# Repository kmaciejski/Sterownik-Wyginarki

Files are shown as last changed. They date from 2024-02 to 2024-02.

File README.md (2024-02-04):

# Projekt sterownika wyginarki do profili stalowych

## Dane Techniczne
- Low cost MCU STM32F030F4P6
- Ekran LCD alfanumeryczny podłączony do magistrali I2C
- Podłączenie klawiatury 12 przyciskowej zrealizowane na 2 rejstrach 74HC166N
- Zewnętrzna pamięć EEPROM na płytce PCB do zapamiętywania ustawień podłączona do magistrali I2C
- Podłączony enkoder z linią Zerującą obsługiwany na przerwaniach
- Wyprowadzone wyjścia przekaźnikowe do sterowania stycznikami silnika i wbudowane przekaźniki na płytce PCB
- Zasilanie zewnętrzne 12V i wbudowane regulatory napięcia dla logiki na płytce PCB

## Możliwości
- Funkcja Automatycznego startu maszyny
- Funkcja Autocofania 
- Funkcja pamięci nastaw (8 różnych nastaw do zapamiętania M1-M8)
- Wielopoziomowe menu
- Zaawansowana obsługa przycisków na klawiaturze m.in. przytrzymanie i autorepetycja

## Działający prototyp







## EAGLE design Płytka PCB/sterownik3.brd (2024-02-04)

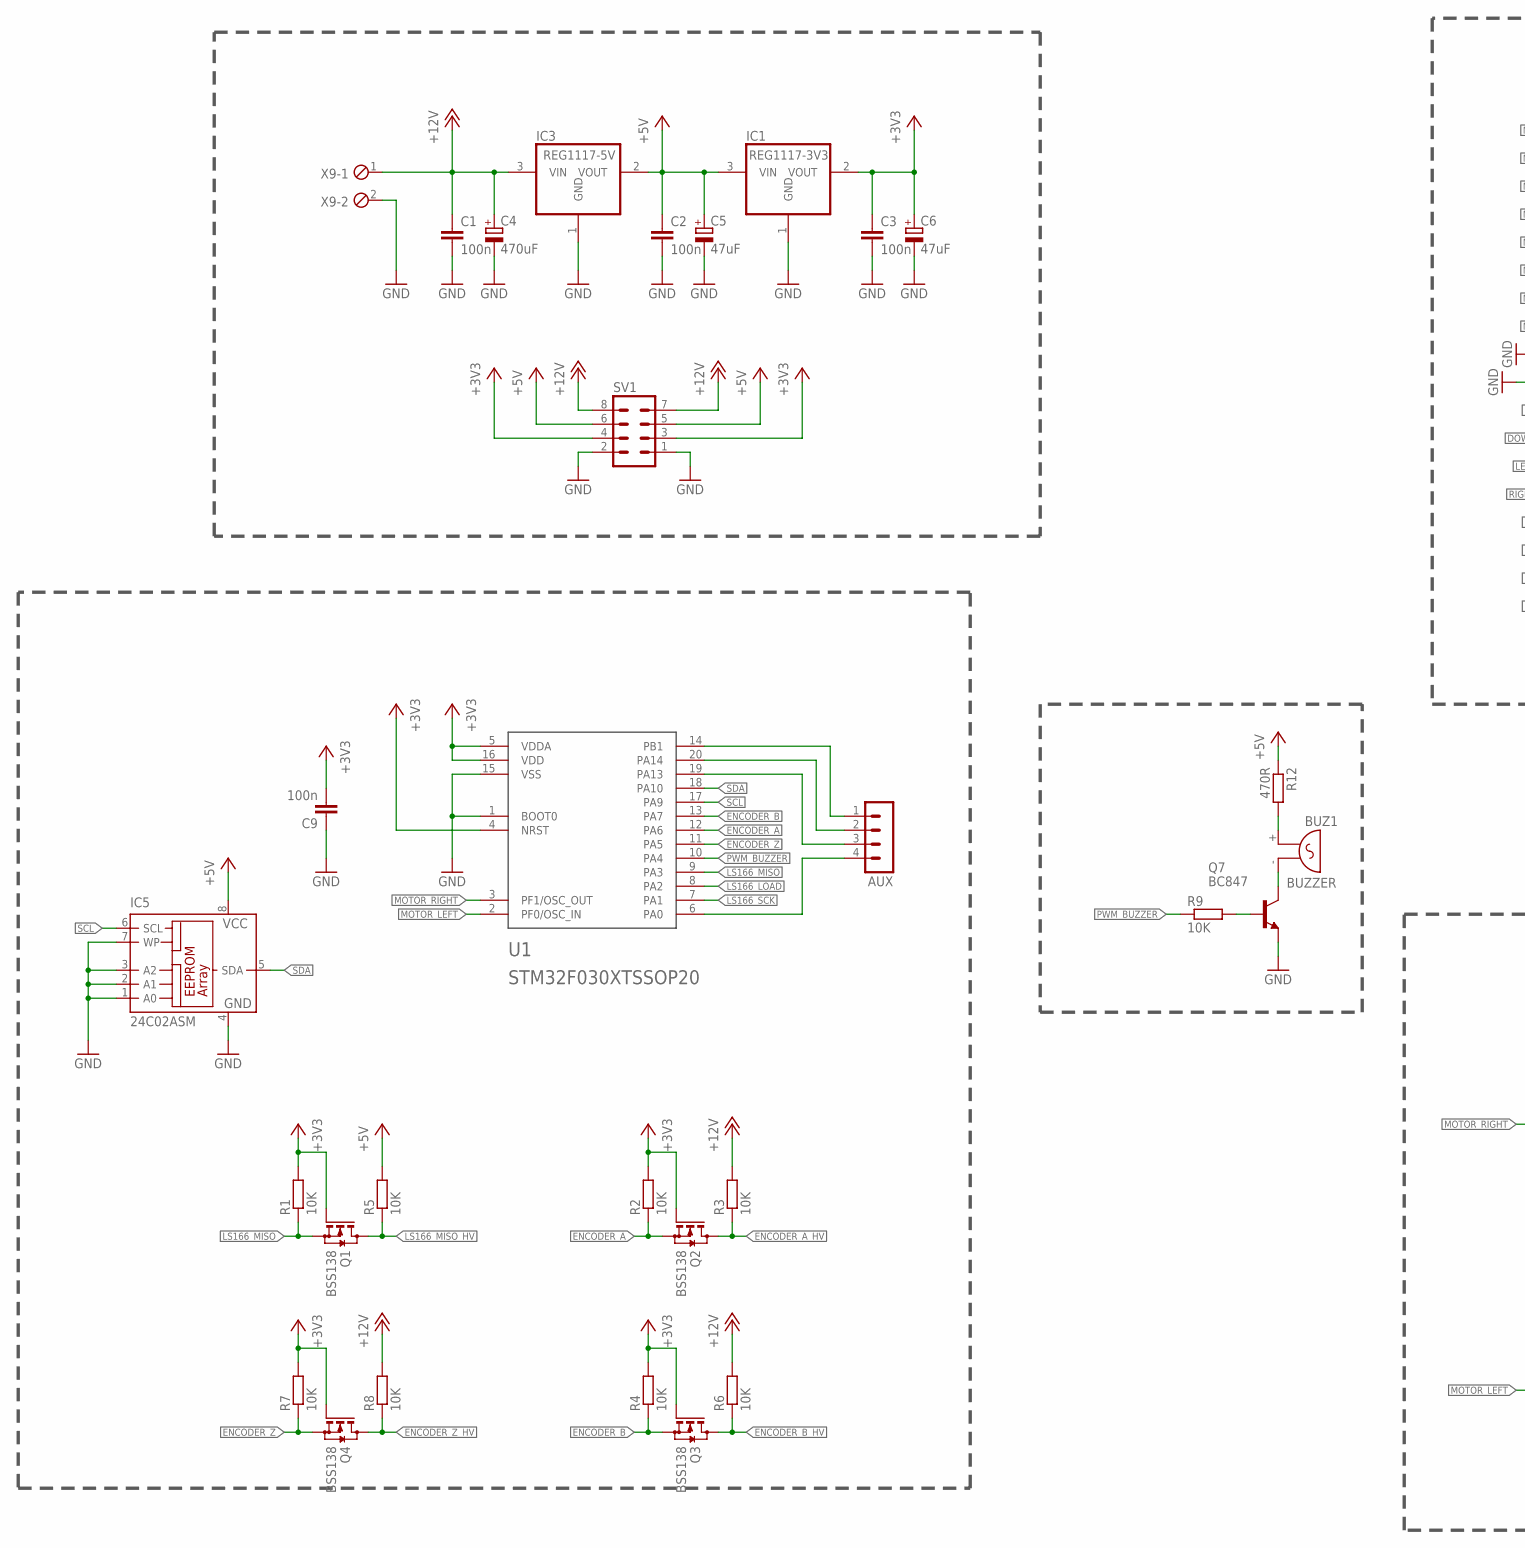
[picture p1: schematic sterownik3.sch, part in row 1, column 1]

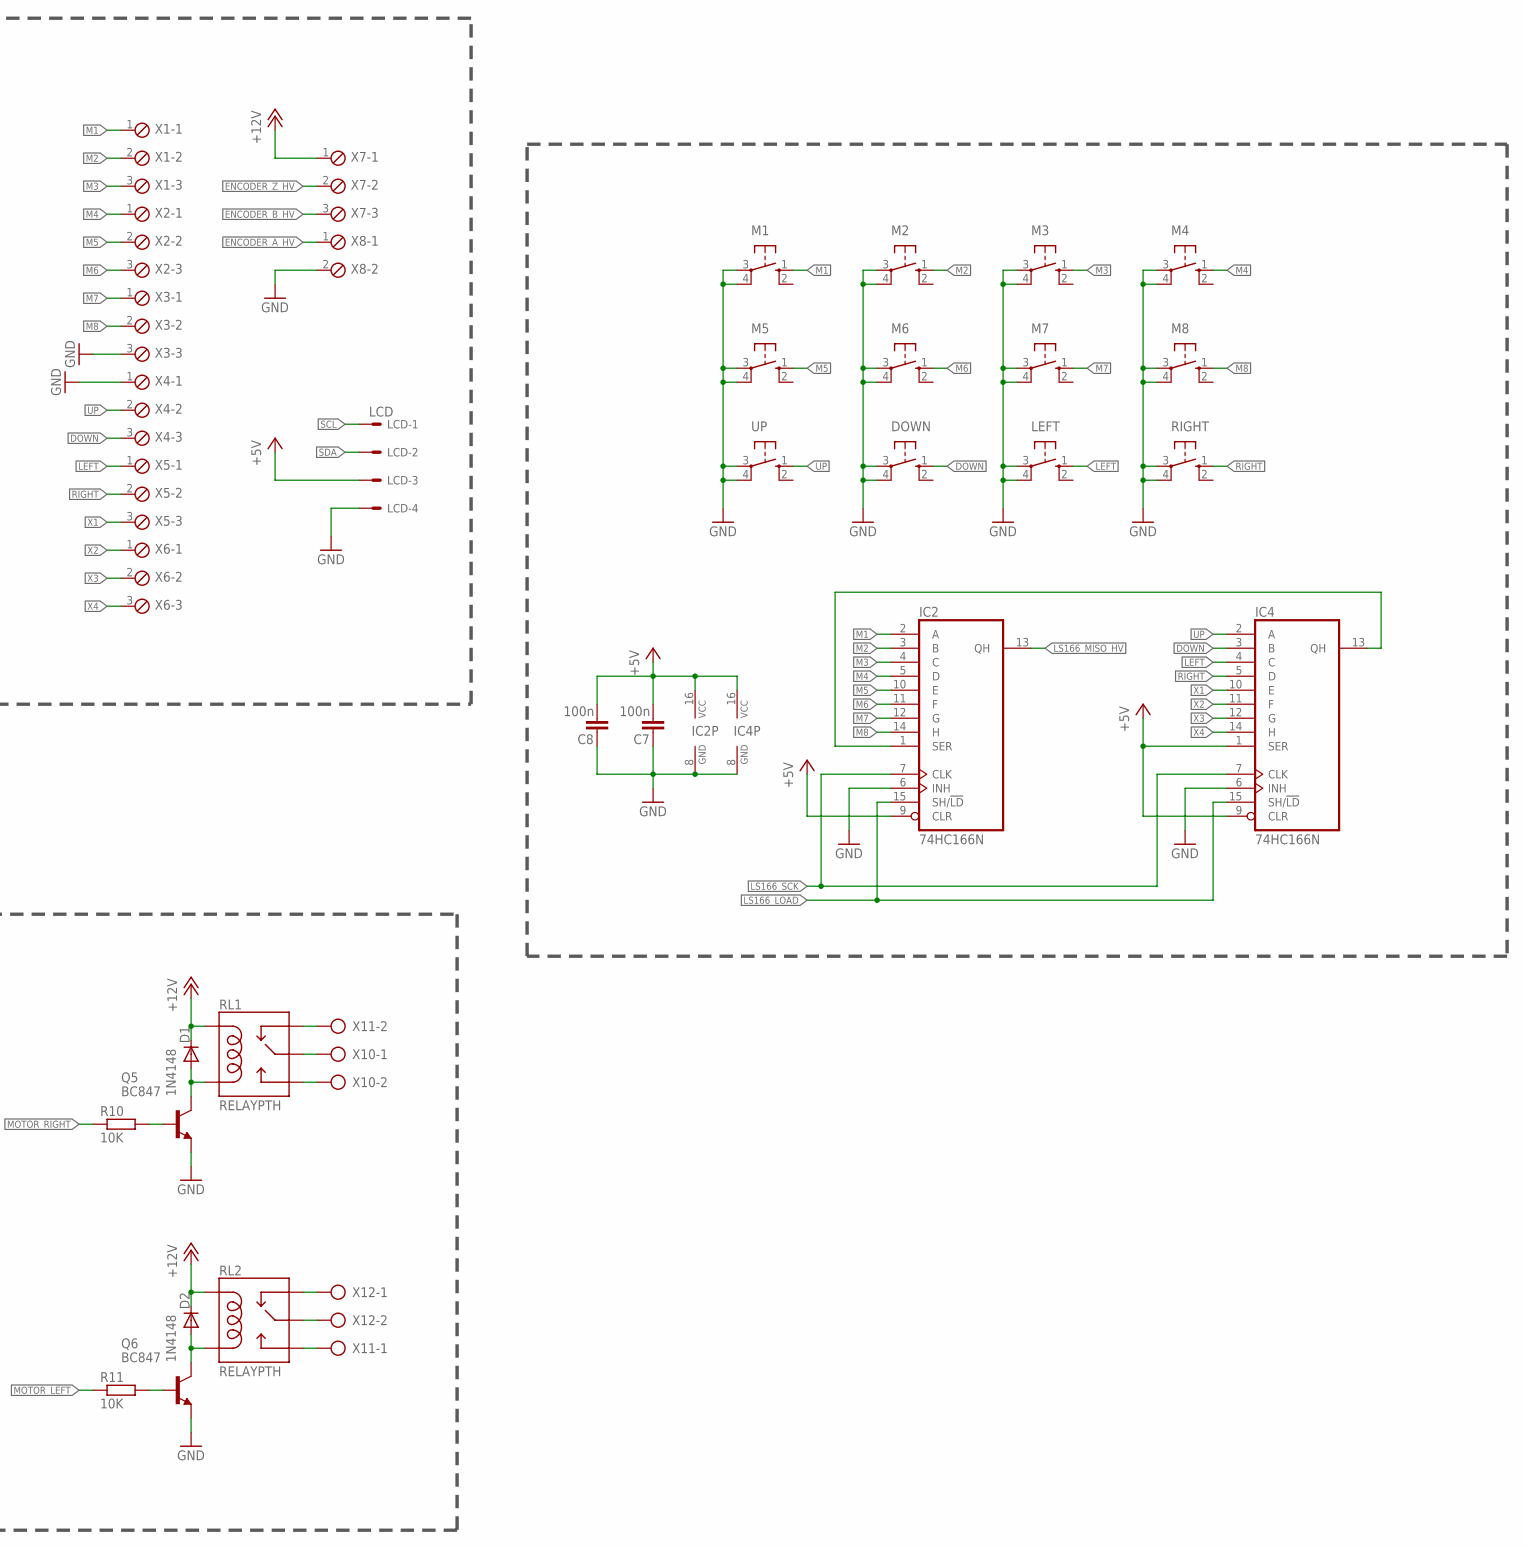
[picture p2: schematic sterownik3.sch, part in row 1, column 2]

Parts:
AUX: MA04-1
BUZ1: BUZZER; F/QMX
C1, C2, C3, C7, C8, C9: 100n; C0805
C4: 470uF; E5-8,5
C5, C6: 47uF; E5-6
D1, D2: 1N4148; DO35-7
DOWN: 10-XX; B3F-10XX
IC1: REG1117-3V3; SOT223
IC2, IC4: 74HC166N; DIL16
IC3: REG1117-5V; SOT223
IC5: 24C02ASM; SO-08M
LCD: LCD; 6410-04
LEFT: 10-XX; B3F-10XX
M1, M2, M3, M4, M5, M6, M7, M8: 10-XX; B3F-10XX
Q1, Q2, Q3, Q4: BSS138; SOT23
Q5, Q6, Q7: BC847; SOT23
R1, R2, R3, R4, R5, R6, R7, R8, R9, R10, R11: 10K; R0805
R12: 470R; R0805
RIGHT: 10-XX; B3F-10XX
RL1, RL2: RELAYPTH; SRD-05VDC-SL-C
SV1: MA04-2
U1: STM32F030XTSSOP20; TSSOP-20
UP: 10-XX; B3F-10XX
X1, X2, X3, X4, X5, X6, X7: MPT3; 3POL254
X8, X9: MPT2; 2POL254
X10, X11, X12: AK500/2

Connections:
+3V3: C3.1, C6.+, C9.2, IC1.2 (VOUT), Q1.1 (G), Q2.1 (G), Q3.1 (G), Q4.1 (G), R1.2, R2.2, R4.2, R7.2, SV1.3, SV1.4, U1.4 (NRST), U1.5 (VDDA), U1.16 (VDD)
+5V: C2.1, C5.+, C7.1, C8.1, IC1.3 (VIN), IC2.9 (CLR), IC2.16 (VCC), IC3.2 (VOUT), IC4.1 (SER), IC4.9 (CLR), IC4.16 (VCC), IC5.8 (VCC), LCD.3, R5.2, R12.1, SV1.5, SV1.6
+12V: C1.1, C4.+, D1.C, D2.C, IC3.3 (VIN), R3.2, R6.2, R8.2, RL1.COIL1, RL2.COIL1, SV1.7, SV1.8, X7.1, X9.1
DOWN: DOWN.1 (S), IC4.3 (B), X4.3
ENCODER_A: Q2.2 (S), R2.1, U1.12 (PA6)
ENCODER_A_HV: Q2.3 (D), R3.1, X8.1
ENCODER_B: Q3.2 (S), R4.1, U1.13 (PA7)
ENCODER_B_HV: Q3.3 (D), R6.1, X7.3
ENCODER_Z: Q4.2 (S), R7.1, U1.11 (PA5)
ENCODER_Z_HV: Q4.3 (D), R8.1, X7.2
GND: C1.2, C2.2, C3.2, C4.-, C5.-, C6.-, C7.2, C8.2, C9.1, DOWN.3, DOWN.4 (P1), IC1.1 (GND), IC2.6 (INH), IC2.8 (GND), IC3.1 (GND), IC4.6 (INH), IC4.8 (GND), IC5.1 (A0), IC5.2 (A1), IC5.3 (A2), IC5.4 (GND), IC5.7 (WP), LCD.4, LEFT.3, LEFT.4 (P1), M1.3, M1.4 (P1), M2.3, M2.4 (P1), M3.3, M3.4 (P1), M4.3, M4.4 (P1), M5.3, M5.4 (P1), M6.3, M6.4 (P1), M7.3, M7.4 (P1), M8.3, M8.4 (P1), Q5.2 (E), Q6.2 (E), Q7.2 (E), RIGHT.3, RIGHT.4 (P1), SV1.1, SV1.2, U1.1 (BOOT0), U1.15 (VSS), UP.3, UP.4 (P1), X3.3, X4.1, X8.2, X9.2
LEFT: IC4.4 (C), LEFT.1 (S), X5.1
LS166_LOAD: IC2.15 (SH/!LD), IC4.15 (SH/!LD), U1.8 (PA2)
LS166_MISO: Q1.2 (S), R1.1, U1.9 (PA3)
LS166_MISO_HV: IC2.13 (QH), Q1.3 (D), R5.1
LS166_SCK: IC2.7 (CLK), IC4.7 (CLK), U1.7 (PA1)
M1: IC2.2 (A), M1.1 (S), X1.1
M2: IC2.3 (B), M2.1 (S), X1.2
M3: IC2.4 (C), M3.1 (S), X1.3
M4: IC2.5 (D), M4.1 (S), X2.1
M5: IC2.10 (E), M5.1 (S), X2.2
M6: IC2.11 (F), M6.1 (S), X2.3
M7: IC2.12 (G), M7.1 (S), X3.1
M8: IC2.14 (H), M8.1 (S), X3.2
MOTOR_LEFT: R11.1, U1.2 (PF0/OSC_IN)
MOTOR_RIGHT: R10.1, U1.3 (PF1/OSC_OUT)
unnamed: AUX.3, U1.19 (PA13)
unnamed: AUX.2, U1.20 (PA14)
unnamed: AUX.1, U1.14 (PB1)
unnamed: AUX.4, U1.6 (PA0)
unnamed: BUZ1.- (1), Q7.3 (C)
unnamed: BUZ1.+ (2), R12.2
unnamed: Q7.1 (B), R9.2
unnamed: Q6.1 (B), R11.2
unnamed: Q5.1 (B), R10.2
unnamed: D1.A, Q5.3 (C), RL1.COIL0
unnamed: D2.A, Q6.3 (C), RL2.COIL0
unnamed: RL2.SWCLOSED (SWCLOSE), X12.1
unnamed: RL1.SWCOMMON, X10.1
unnamed: RL2.SWOPEN, X11.1
unnamed: RL1.SWCLOSED (SWCLOSE), X11.2
unnamed: RL2.SWCOMMON, X12.2
unnamed: RL1.SWOPEN, X10.2
unnamed: IC2.1 (SER), IC4.13 (QH)
PWM_BUZZER: R9.1, U1.10 (PA4)
RIGHT: IC4.5 (D), RIGHT.1 (S), X5.2
SCL: IC5.6 (SCL), LCD.1, U1.17 (PA9)
SDA: IC5.5 (SDA), LCD.2, U1.18 (PA10)
UP: IC4.2 (A), UP.1 (S), X4.2
X1: IC4.10 (E), X5.3
X2: IC4.11 (F), X6.1
X3: IC4.12 (G), X6.2
X4: IC4.14 (H), X6.3

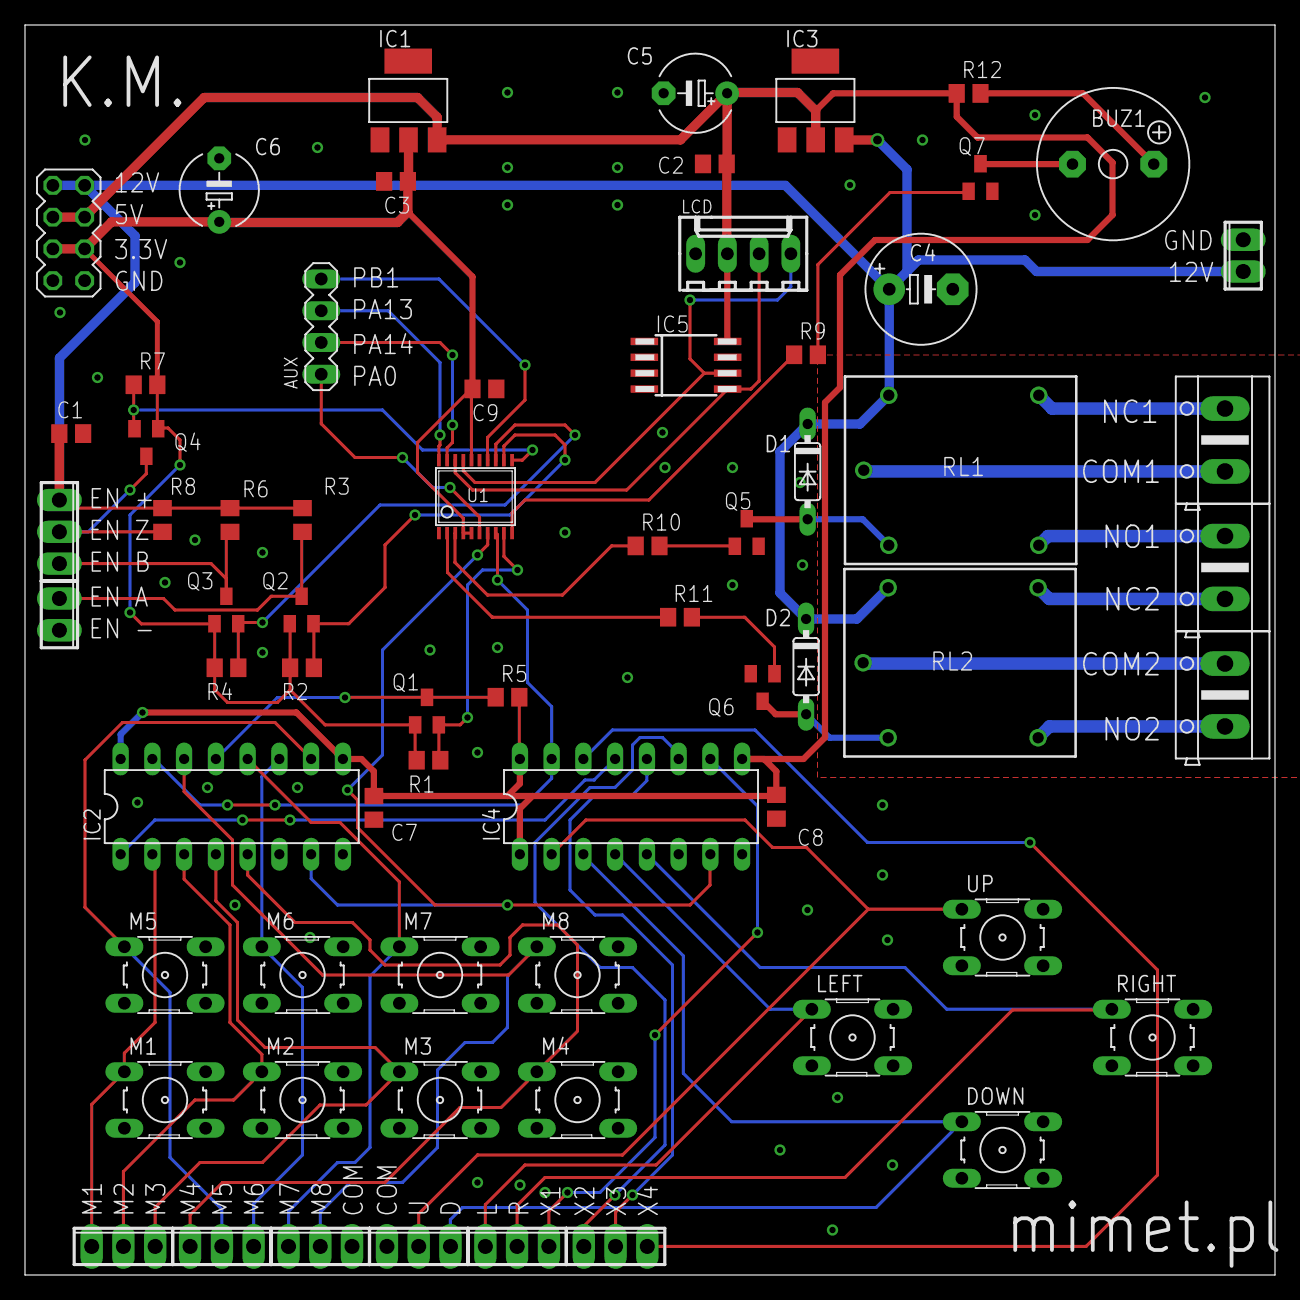
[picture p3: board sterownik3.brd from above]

Board: 2 copper layers, 100.0 x 100.0 mm, 66 parts (0 on the bottom side), 53 nets.

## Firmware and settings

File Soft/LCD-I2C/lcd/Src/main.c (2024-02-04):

/**
  ******************************************************************************
  * @file           : main.c
  * @brief          : Main program body
  ******************************************************************************
  ** This notice applies to any and all portions of this file
  * that are not between comment pairs USER CODE BEGIN and
  * USER CODE END. Other portions of this file, whether 
  * inserted by the user or by software development tools
  * are owned by their respective copyright owners.
  *
  * COPYRIGHT(c) 2018 STMicroelectronics
  *
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
  ******************************************************************************
  */
/* Includes ------------------------------------------------------------------*/
#include "main.h"
#include "stm32f4xx_hal.h"

/* USER CODE BEGIN Includes */
#include "i2c-lcd.h"
/* USER CODE END Includes */

I2C_HandleTypeDef hi2c1;

/* USER CODE BEGIN PV */

/* USER CODE END PV */

void SystemClock_Config(void);
static void MX_GPIO_Init(void);
static void MX_I2C1_Init(void);

/* USER CODE BEGIN PFP */

/* USER CODE END PFP */

/**
  * @brief  The application entry point.
  *
  * @retval None
  */
int main(void)
{
  /* MCU Configuration----------------------------------------------------------*/

  /* Reset of all peripherals, Initializes the Flash interface and the Systick. */
  HAL_Init();

  /* Configure the system clock */
  SystemClock_Config();

  /* Initialize all configured peripherals */
  MX_GPIO_Init();
  MX_I2C1_Init();
  /* USER CODE BEGIN 2 */

	lcd_init ();
	
	lcd_send_string ("HELLO WORLD !!");
  /* USER CODE END 2 */

  /* Infinite loop */
  /* USER CODE BEGIN WHILE */
  while (1)
  {

  /* USER CODE END WHILE */

  /* USER CODE BEGIN 3 */
		lcd_send_cmd (0x80);  // goto 1,1
		
		lcd_send_string ("subscribe");
		
		lcd_send_cmd (0xc0);
		
		lcd_send_string ("to this channel");
		
		HAL_Delay (2000);  // wait for 2 sec
		
		lcd_send_cmd (0x01);  // clear the display
		
		HAL_Delay (1000);
		
  }
  /* USER CODE END 3 */

}

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


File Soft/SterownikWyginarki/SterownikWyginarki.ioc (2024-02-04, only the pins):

Mcu.UserName=STM32F030F4Px
PA1.GPIO_Label=LS166_SCK
PA1.Signal=GPIO_Output
PA10.Signal=I2C1_SDA
PA2.GPIO_Label=LS166_LOAD
PA2.Signal=GPIO_Output
PA3.GPIO_Label=LS166_MISO
PA3.Signal=GPIO_Input
PA4.GPIO_Label=PWM_BUZZER
PA4.Signal=S_TIM14_CH1
PA5.GPIO_Label=ENCODER_Z
PA5.Signal=GPXTI5
PA6.GPIO_Label=ENCODER_A
PA6.Signal=S_TIM3_CH1
PA7.GPIO_Label=ENCODER_B
PA7.Signal=S_TIM3_CH2
PA9.Signal=I2C1_SCL
PF0-OSC_IN.GPIO_Label=MOTOR_LEFT
PF0-OSC_IN.Signal=GPIO_Output
PF1-OSC_OUT.GPIO_Label=MOTOR_RIGHT
PF1-OSC_OUT.Signal=GPIO_Output

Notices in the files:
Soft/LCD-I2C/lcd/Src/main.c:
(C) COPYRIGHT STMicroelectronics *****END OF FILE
